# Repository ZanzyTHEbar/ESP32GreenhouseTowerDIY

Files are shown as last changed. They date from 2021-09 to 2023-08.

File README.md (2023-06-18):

   

# :seedling: ESP32GreenhouseTowerDIY :seedling:

This repo is dedicated to the **DIY ESP32** based automated *Aeroponic* or *Hydroponic* Modular Tower Garden :cactus: .

# WHAT IS THIS PROJECT

In the height of COVID I wanted to grow my own food indoors. This open source project is a culmination of my own work and many inspirations from the internet to develop an easy, approachable and beginner friendly project for hobbyists.

This project is designed to be modular and affordable. Featuring a vertical tower system with interlocking parts and an adapter to a common `20L/5gallon` bucket.

The design also features an optional 3D printable Aeroponics Nozzle for converting the system from hydroponic to aeroponics.  

> I originally decided to go with an ESP32 using Micropython firmware. While Arduino is perfectly fine, i wanted this project to be approachable to all skill levels, python seemed like the most common first "language". However, I since realized that most people who use this _won't_ be coding themselves and i prefer C++ more than python, so I switched the entire project over and am building a website to flash the boards. Users will not need to download any code themselves. Please stay tuned for the documentation website.  
>
> **Note**: I have added Arduino Core support for the ESP32. This is a work in progress and will is now the main code-base. It simply has more sensor support, a few more features, and it runs faster/consumes less power.

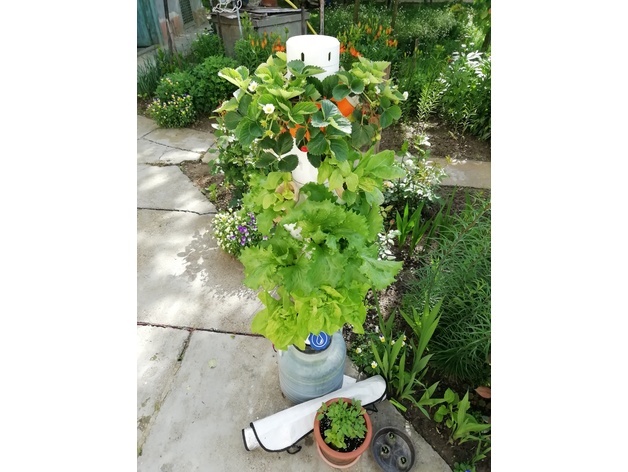
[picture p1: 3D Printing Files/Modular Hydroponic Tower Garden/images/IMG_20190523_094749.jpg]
tower garden


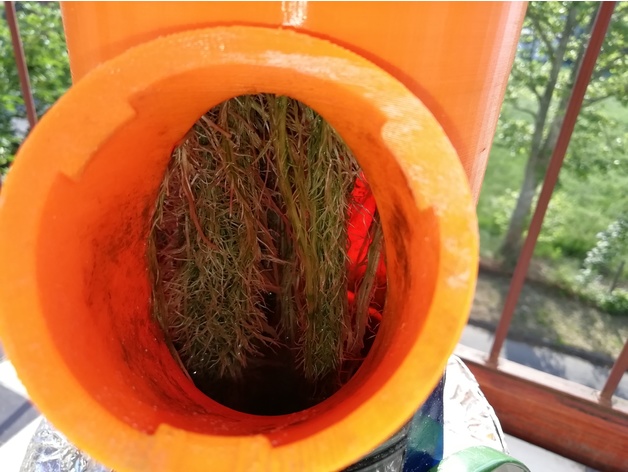
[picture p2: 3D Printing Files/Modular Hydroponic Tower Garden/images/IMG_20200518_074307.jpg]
tower garden


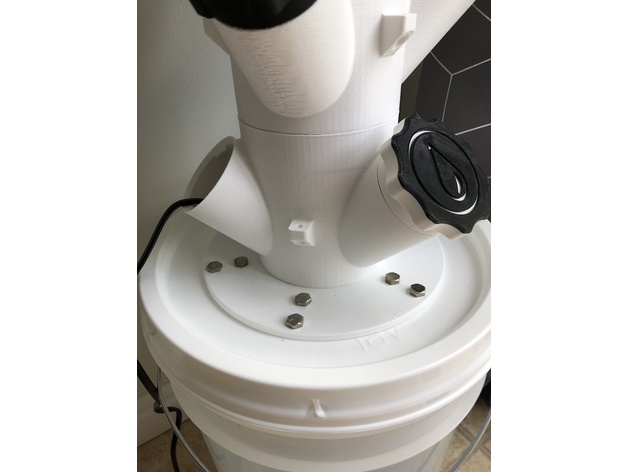
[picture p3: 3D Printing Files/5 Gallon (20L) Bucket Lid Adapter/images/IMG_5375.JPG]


# HOW TO ORDER PCBS

PCBS can be ordered from [JLCPCB](https://jlcpcb.com/) or [PCBWay](https://www.pcbway.com/), or made yourself. The PCB files are still in prototype phase and I welcome any development ideas.

# Introduction

**Purpose:** These are instructions to build an open hardware, DIY Vertical Greenhouse Garden.

**Expected results:** A fully functional and (reasonably) automated vertical tower system.

**Minimal parts cost:** `<$20` for the basic system which consists of a `20L/5gallon` (can be smaller - minimum size is `4L/1gallon`) humidifier box/water reservoir and submersible pump - about `$100`. You will also need to purchase the PCB's `~$40`, power supply and sensors `~$30`. The cost of the parts will vary depending on the size of the tower, and the number of sensors. The cost of 3D printing the tower will be `~$25` or less. The full `1m` tower consumes `~2kg` of `PETG` - which is the recommended printing material for outdoor use. The tower can be printed in `ABS` and/or `PETG` materials.

> **Note**: The cost of plant nutrients is not taken into account, and is up to you to control.

**Goal:** The goal of this project was to build a high-efficiency, very low cost direct DIY vertical tower garden for growing small fruits and vegetables.

____

> **Warning**: The sections below are experimental docs and are subject to change. Please wait for the documentation website to be finished if you want a consistent experience.

## How to Setup  - Hardware

Setup is very straight forward, thankfully. You will need to purchase a few components before you begin:

### ***Materials for purchase***

1. Raspberrypi - *any model*
   1. Install the MQTT client included with Home Assistant (install Home Assistant), as this project has full support for Home Assistant (Arduino Core version only currently).
      1. Alternatively, you can install Mosquitto broker to the pi and connect it to your network
2. 12V submersible water pump
3. 3m or more of Vinyl tubing with 10mm ID and 13mm OD

____

## How to Setup - Software

1. Acquire all parts and ESP32 (WROVER and WROOM (S3 versions are supported) have both been tested).
2. Acquire The remaining sensors and components - assemble

### ***SETUP***

____

#### Micropython

1. Plug ESP32 into computer - open your IDE (i used Thonny for this project) Flash the micropython firmware to the esp32
   1. Upload ESP32MicropytyhonLibraries ---> rename to ESP32Micro
   2. Upload boot.py and greenhouse.py to root directory

____

#### Arduino Core

1. Plug ESP32 into computer - navigate to [WebSerial](/ESP32GreenhouseTowerDIY/webserial/)
   1. Configure your chosen sensors and features
   2. Press build and upload, and wait for the green light to turn on - it is safe to unplug the ESP32 at that point.

____

#### MQTT Broker Configuration and Connection

If you have chosen the mDNS option, you will need to setup mDNS on your network for MQTT Discovery. The mDNS service on the ESP is already configure, if you chose that feature, and should appear on your network as at the `<name>.tower.local` address.

The MQTT Broker is a free service that allows you to publish and subscribe to MQTT messages. To automate the connection process, this project offers Multi-Cast DNS (mDNS/Zeroconf) to find the broker. For this to work, you must have a broker on your local network, and you must have only 1 MQTT broker within the range of the client, otherwise the client will simply connect to the images broker it finds.

Using a Zeroconf approach we can avoid having to hard code the broker's IP address or hostname into the client device's firmware. Instead we can use DNS-SD and Avahi/Bonjour to discover the server hosting the MQTT broker.

To enable MQTT discovery on the broker, simply install avahi-daemon.

##### Option One:

If you are using Home Assistant, you can use the MQTT Discovery feature within the firmware, and the MQTT broker will be discovered automatically. Nothing is needed from you for this to work. Simply turn on the ESP32 and have the `mDNS` feature enabled in the firmware.

You can refer to the [ZeroConf Documentation here](https://www.home-assistant.io/integrations/zeroconf/) and [here](https://developers.home-assistant.io/docs/creating_integration_manifest/#zeroconf) for home assistance for more information and troubleshooting.

If for some reason you are unable to use the MQTT Discovery feature, you can still use the mDNS feature to discover the broker, see Option Two below.

##### Option Two:

You will need to install the [avahi](https://avahi.org/) package. For a Raspberry Pi, use the following command:

    sudo apt-get install avahi-daemon

For this to work, the MQTT service needs to be advertised. On a Linux host system, Avahi can be configured to do this by including the following in `/etc/avahi/services/mqtt.service`:

```xml
<!DOCTYPE service-group SYSTEM "avahi-service.dtd">
<service-group>
 <name replace-wildcards="yes">MQTT on %h</name>
  <service>
   <type>_mqtt._tcp</type>
   <port>1883</port>
  </service>
</service-group>
```

____

## Benefits

____

## Challenges and Limitations

____

## Safety Considerations

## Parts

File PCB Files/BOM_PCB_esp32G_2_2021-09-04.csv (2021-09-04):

ID | Name | Designator | Footprint | Quantity | Manufacturer Part | Manufacturer | Supplier | Supplier Part | Price | Pins | 3DModel | JLCPCB Part Class | Paste Type | Contributor | description | license | link
1 | PIN_Female_2 | DATA,POWER,U3,U6,U7 | PIN_CONNECTOR_2 | 5 | Buchsenleiste Femaile 24 |  |  |  |  | 2 |  |  |  | Florian1
2 | LL4148 | D6,D7,D8 | LL-34_L3.5-W1.5-RD-1 | 3 | LL4148 | SEMTECH | LCSC | C9808 | 0.007 | 2 | LL-34_L3.7-W1.6 | Basic Part |  | jiaowoxiaolu |  |  | https://item.szlcsc.com/289405.html
3 | PIN_Female_4 | U4 | PIN_CONNECTOR_2 | 1 | Buchsenleiste Femaile 24 |  |  |  |  | 2 |  |  |  | Florian1
4 | Header-Female-2.54_1x20 | P6,P7 | HDR-TH_20P-P2.54-V-F | 2 | 2.54mm 1*20P Female header | BOOMELE | LCSC | C50984 | 0.124 | 20 | HDR-F-2.54_1x20 | Extended Part |  | 立创EDA官方封装库 |  |  | https://item.szlcsc.com/316177.html
5 | TERMINAL_3P/5.08 | P1,P4,P5 | 5.08-3P_SCREW_TERMINAL | 3 | Screw terminal 3p |  |  |  |  | 3 |  |  |  | reino.forward
6 | TERMINAL_2P/5.08 | P2,P3 | 5.08-2P_SCREW_TERMINAL | 2 | Screw terminal 2p |  |  |  |  | 2 |  |  |  | Giuseppe Fusi
7 | 1N4007 | D4,D5 | DO-41_BD2.4-L4.7-P8.70-D0.9-RD | 2 | 1N4007 | SEMTECH | LCSC | C106903 | 0.015 | 2 | DO-41_D2.4-L4.7-P8.70 | Extended Part |  | 官方封装库 |  |  | https://item.szlcsc.com/85412.html
8 | 2N3904(SOT-23) | Q1,Q2 | SOT-23-3_L2.9-W1.3-P1.90-LS2.4-TR | 2 | 2n3904S-RTK/PS | KEC | LCSC | C18536 | 0.016 | 3 | SOT-23-3P_L2.9-W1.3-H1.0-LS2.4-P0.95 |  | SOT-23 | 立创EDA官方封装库 |  |  | https://item.szlcsc.com/70837.html
9 | LDR07 | R1 | RESISTOR_LDR_5.1X4.3_RM3.4 | 1 |  |  |  |  |  | 2 |  |  |  | KiCAD |  | https://www.gnu.org/licenses/lgpl-2.1.html
10 | 10k | R2,R3,R4,R5 | R0603 | 4 |  |  |  |  |  | 2 | R0603_L1.6-W0.8-H0.8 |  |  | 立创EDA官方封装库 |  |  | https://www.mouser.in/datasheet/2/447/PYu_RT_1_to_0_01_RoHS_L_11-1669912.pdf
11 | DHT11 | U5 | SENSOR-TH_DHT11 | 1 | CHT11 | CYBERSEN | LCSC | C476208 | 1.559 | 4 | SENSOR-TH_DHT11 | Extended Part |  | 立创EDA官方封装库 |  |  | https://list.szlcsc.com/catalog/922.html
12 | JQC-3FF-S-Z | U8,U9 | JQC-3FF-S-Z | 2 | JQC-3FF-S-Z |  |  |  |  | 5 |  |  |  | EasyEDA |  |  | https://www.alibaba.com/product-detail/relay-types-JQC-3FF-S-Z_60682592473.html
13 | LED-TH-5mm_R | LED1 | LED-TH_BD5.0_RED | 1 | 333-2SURD/S530-A3 | EVERLIGHT(台湾亿光) | LCSC | C87271 | 0.035 | 2 | LED-TH_BD5.0_Red |  |  | LCEDA_Lib
14 | LED-TH-5mm_G | LED2 | LED-TH_BD5.0_GREEN | 1 | 333-2SYGD/S530-E2 | EVERLIGHT(台湾亿光) | LCSC | C88163 | 0.037 | 2 | LED-TH_BD5.0_Green |  |  | LCEDA_Lib
15 | LED-TH-5mm_B | LED3 | LED-TH_BD5.0_BLUE | 1 |  |  | LCSC |  |  | 2 | LED-TH_BD5.0_Blue |  |  | LCEDA_Lib
16 | 220Ohm | R6,R7,R8 | R0603 | 3 |  |  |  |  |  | 2 | R0603_L1.6-W0.8-H0.8 |  |  | LCEDA_Lib |  |  | https://www.mouser.in/datasheet/2/447/PYu_RT_1_to_0_01_RoHS_L_11-1669912.pdf

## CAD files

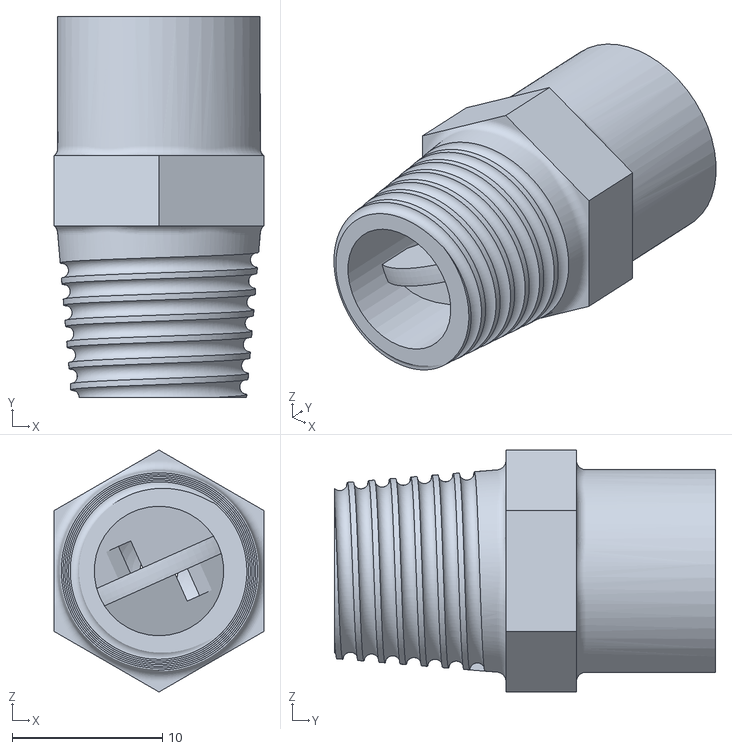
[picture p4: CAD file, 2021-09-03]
3D Printing Files/Aeroponic Misting Nozzles/files/Full_cone_spray_nozzle.STL
14.0 x 25.4 x 16.1

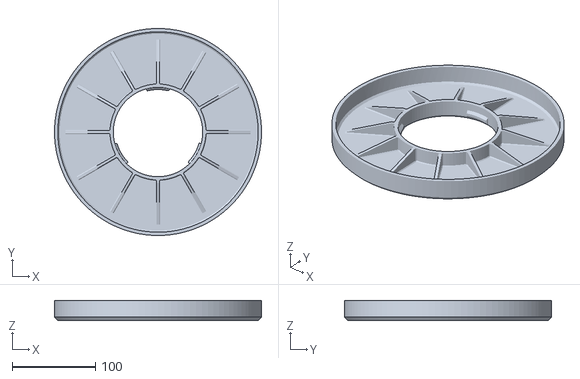
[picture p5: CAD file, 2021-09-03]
3D Printing Files/Modular Hydroponic Tower Garden/files/IKEA_Muskot_Pot_7_12_Adapter_ID240mm_Full.STL
248.0 x 248.0 x 24.0

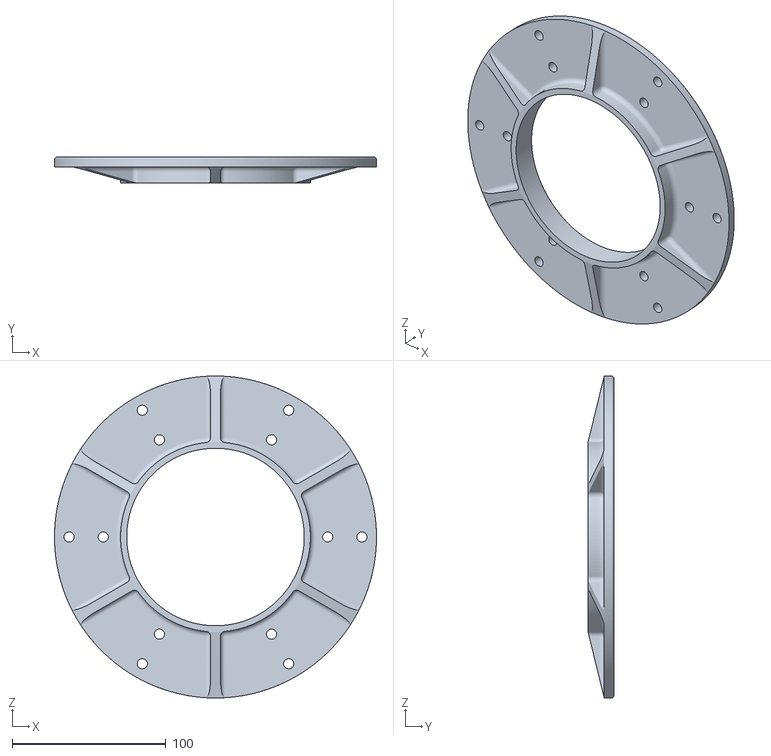
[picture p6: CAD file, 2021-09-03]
3D Printing Files/5 Gallon (20L) Bucket Lid Adapter/files/5_gallon_bucket_lid_Bottom_Adapter.STL
209.5 x 16.9 x 209.5

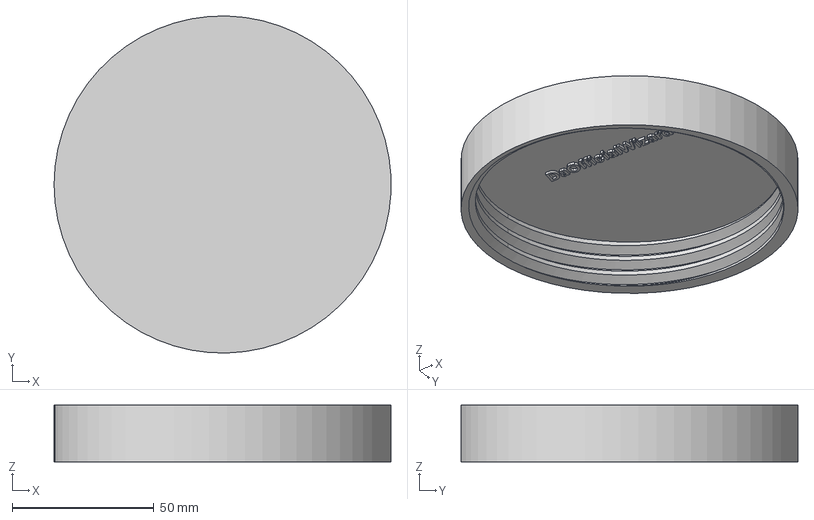
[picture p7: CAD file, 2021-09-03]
3D Printing Files/Aeroponic Misting Nozzles/files/lid v1.step
118.9 x 119.0 x 20.0 mm

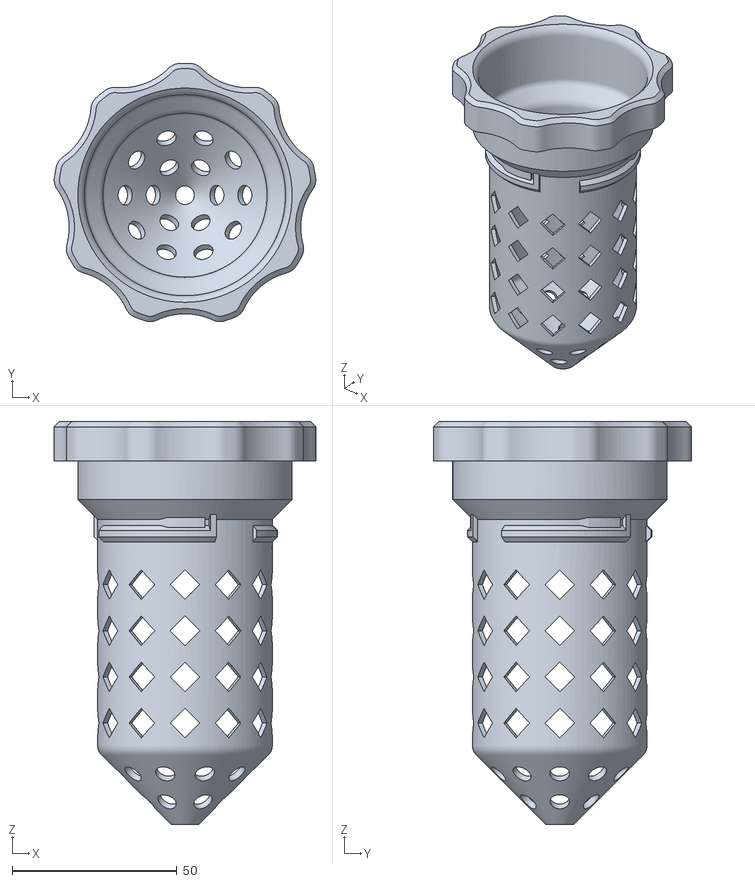
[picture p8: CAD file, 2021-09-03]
3D Printing Files/Modular Hydroponic Tower Garden/files/Standard_Pot_02.STL
79.4 x 78.4 x 122.3

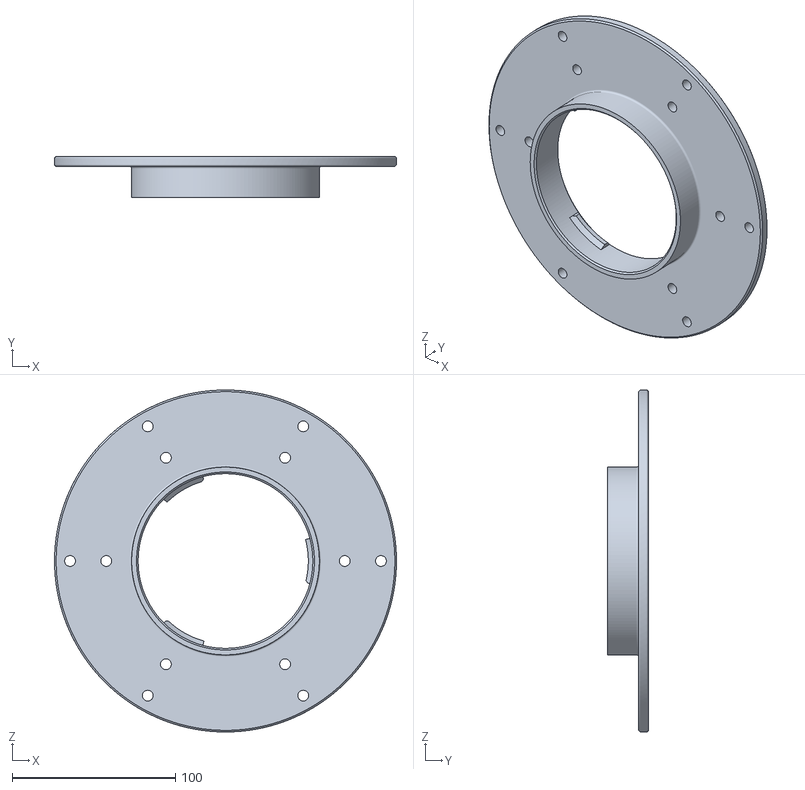
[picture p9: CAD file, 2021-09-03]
3D Printing Files/5 Gallon (20L) Bucket Lid Adapter/files/5_gallon_bucket_lid_Top_Adapter.STL
209.5 x 25.4 x 209.5

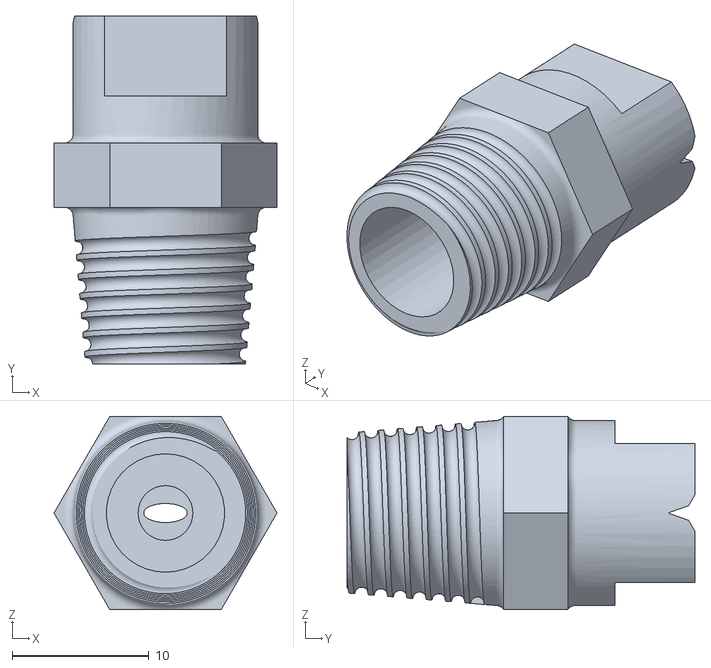
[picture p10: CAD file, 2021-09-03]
3D Printing Files/Aeroponic Misting Nozzles/files/Flat_spray_nozzle.STL
16.3 x 25.4 x 14.1

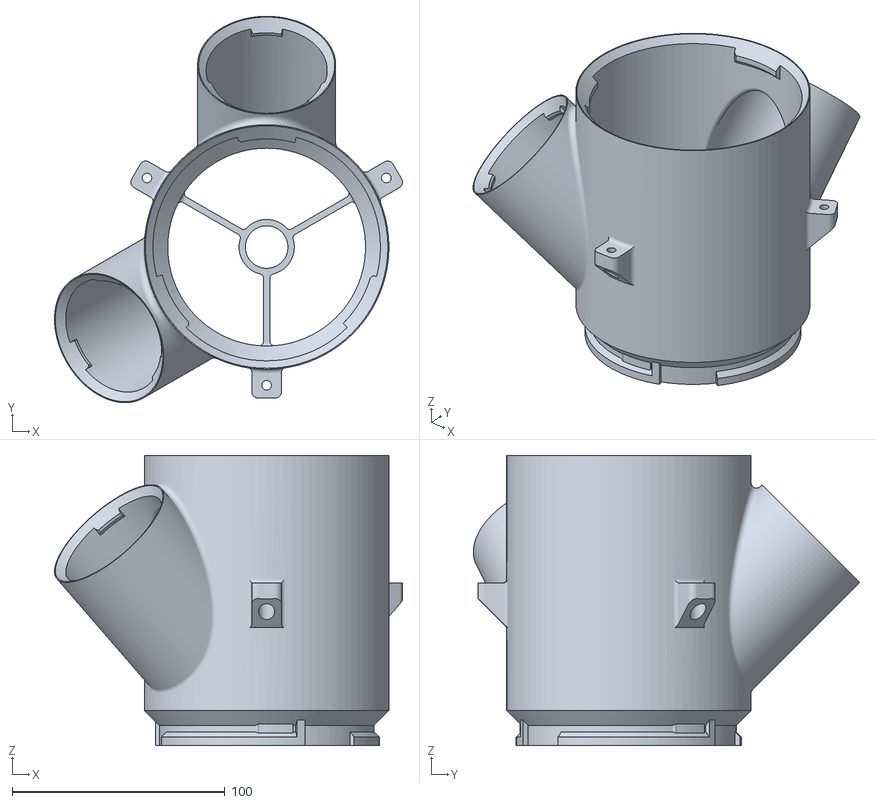
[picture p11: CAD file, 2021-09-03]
3D Printing Files/Modular Hydroponic Tower Garden/files/2-Way_Planting_Module_Hollow.STL
163.7 x 181.7 x 136.5

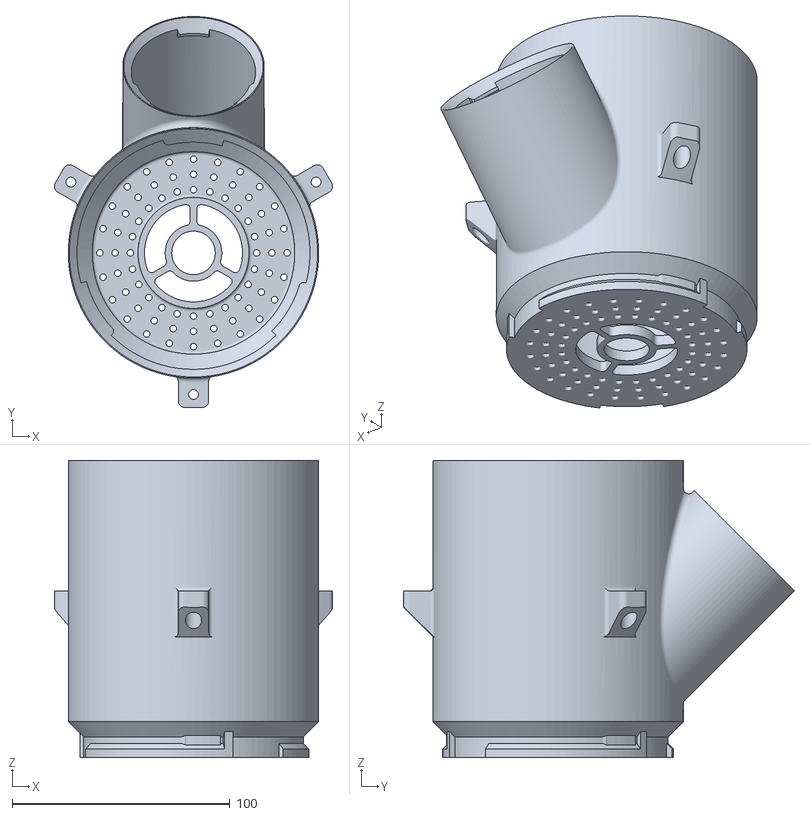
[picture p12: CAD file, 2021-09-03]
3D Printing Files/Modular Hydroponic Tower Garden/files/1-Way_Planting_Module.STL
127.8 x 179.5 x 136.5

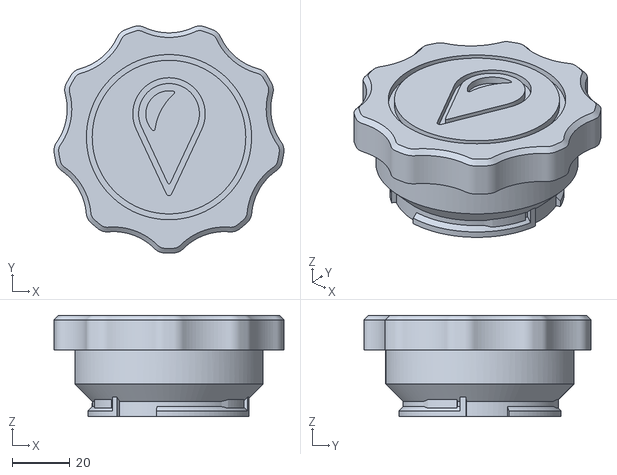
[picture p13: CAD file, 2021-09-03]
3D Printing Files/Modular Hydroponic Tower Garden/files/Filling_Cap.STL
79.4 x 78.4 x 35.0

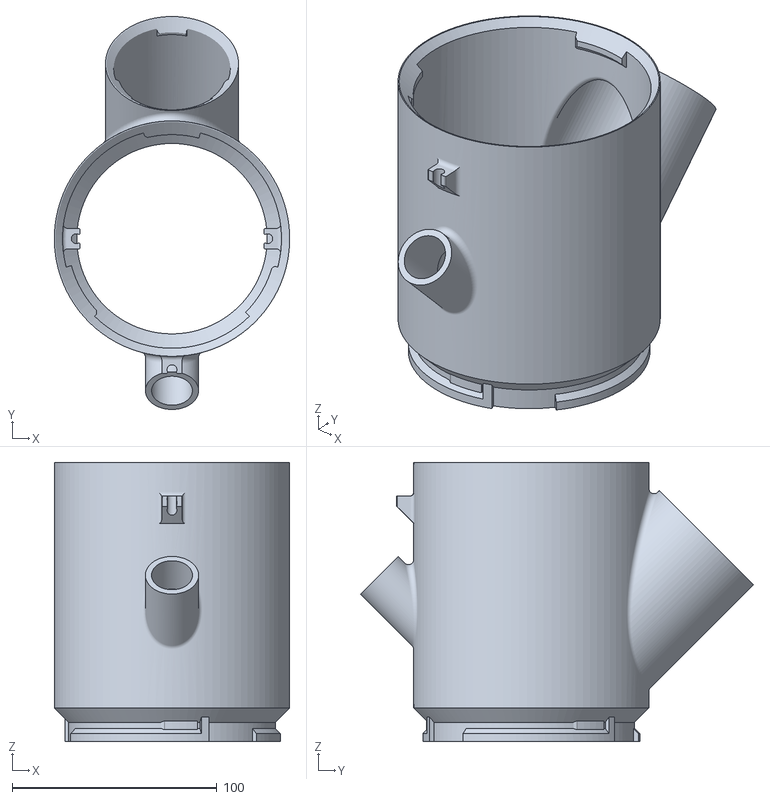
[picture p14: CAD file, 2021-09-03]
3D Printing Files/Modular Hydroponic Tower Garden/files/Filling_Module_mod_01.STL
114.9 x 192.0 x 136.5

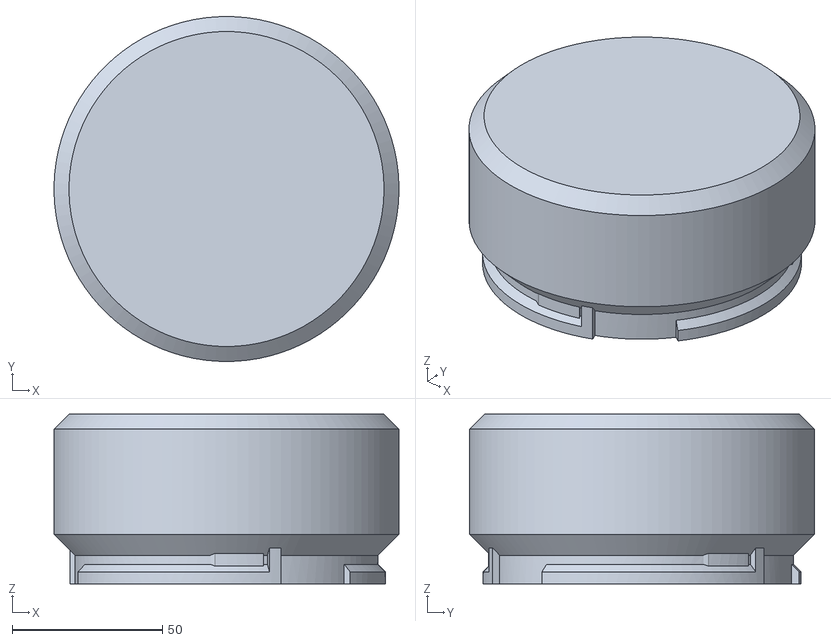
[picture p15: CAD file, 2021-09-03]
3D Printing Files/Modular Hydroponic Tower Garden/files/Lid_Without_Holes.STL
114.9 x 115.0 x 56.5

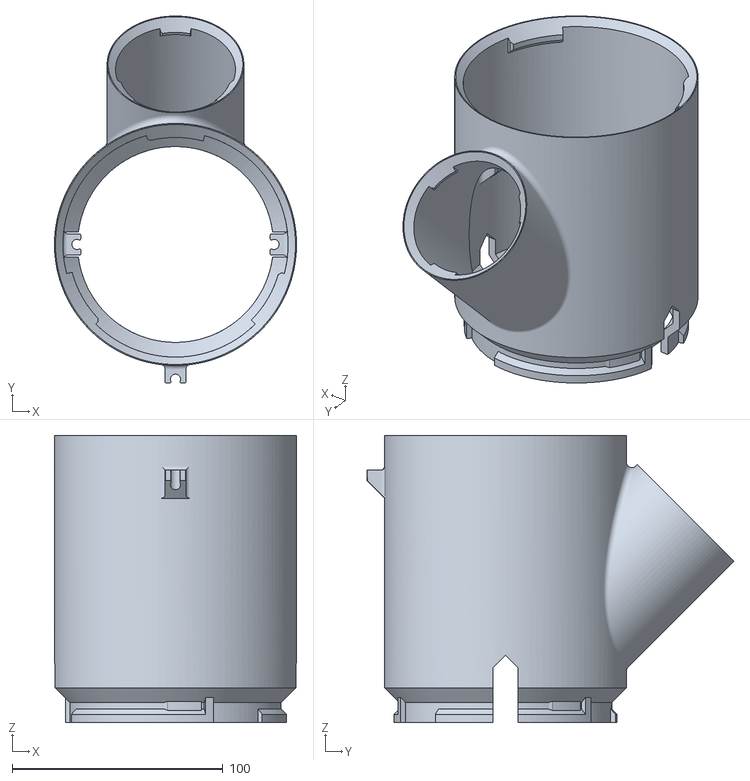
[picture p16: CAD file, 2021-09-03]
3D Printing Files/Modular Hydroponic Tower Garden/files/Filling_Module_Cut_mod_01.STL
115.0 x 174.3 x 136.5

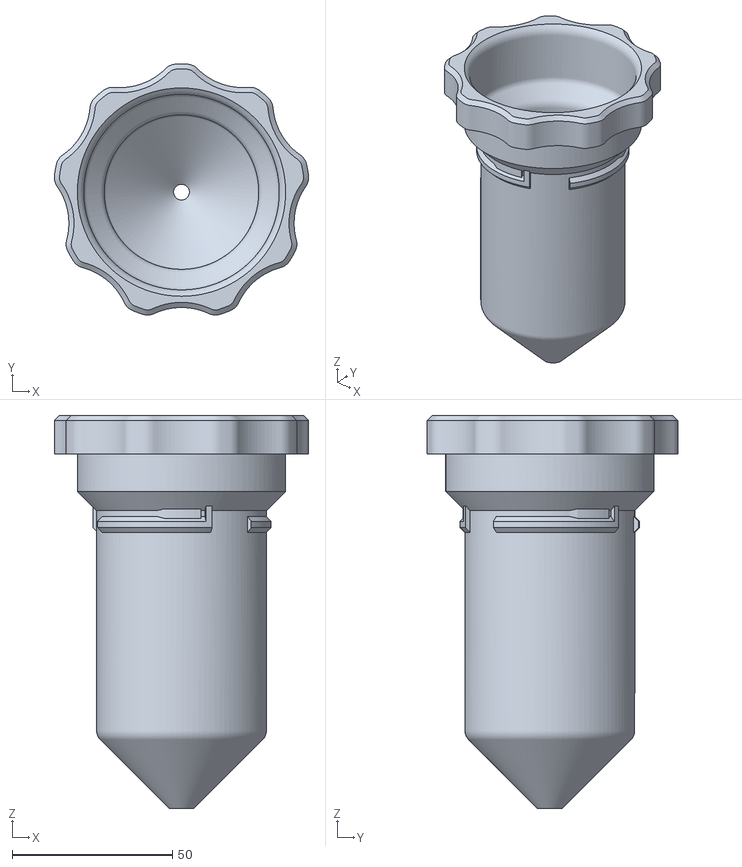
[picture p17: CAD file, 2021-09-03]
3D Printing Files/Modular Hydroponic Tower Garden/files/Standard_Pot_Raw.STL
79.4 x 78.4 x 122.6

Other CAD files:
3D Printing Files/Modular Hydroponic Tower Garden/files/2-Way_Planting_Module_Hollow_Without_M3.STL
3D Printing Files/Modular Hydroponic Tower Garden/files/Jiffy-7_41_Pot_For_4-5-Way_Planting_Module.STL
3D Printing Files/Modular Hydroponic Tower Garden/files/Module_Spacer_40mm.STL
3D Printing Files/Modular Hydroponic Tower Garden/files/Blank_Cap.STL
3D Printing Files/Modular Hydroponic Tower Garden/files/1-Way_Planting_Module_Hollow.STL
3D Printing Files/Modular Hydroponic Tower Garden/files/1-Way_Planting_Module_Hollow_Without_M3.STL
3D Printing Files/Modular Hydroponic Tower Garden/files/3-Way_Planting_Module_Hollow.STL
3D Printing Files/Modular Hydroponic Tower Garden/files/3-Way_Planting_Module_Hollow_Without_M3.STL
3D Printing Files/Modular Hydroponic Tower Garden/files/4-Way_Planting_Module_Hollow.STL
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

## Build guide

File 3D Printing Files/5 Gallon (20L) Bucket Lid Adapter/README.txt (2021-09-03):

5 Gallon Bucket Lid Adapter Plates by Trevorhirschi on Thingiverse: https://www.thingiverse.com/thing:4395675

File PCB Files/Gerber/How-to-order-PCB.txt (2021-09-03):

How to Order PCB

Please refer to:
https://docs.easyeda.com/en/PCB/Order-PCB

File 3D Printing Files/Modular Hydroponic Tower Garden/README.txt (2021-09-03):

Modular Hydroponic Tower Garden by boundarycondition on Thingiverse: https://www.thingiverse.com/thing:3405964

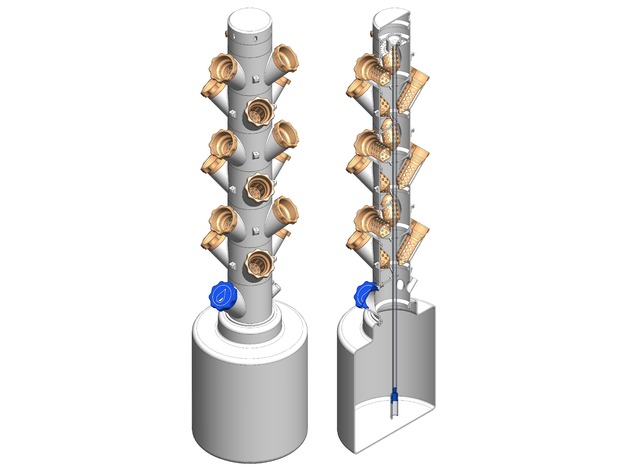
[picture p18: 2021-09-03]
3D Printing Files/Modular Hydroponic Tower Garden/images/MHTG_V113_03.png

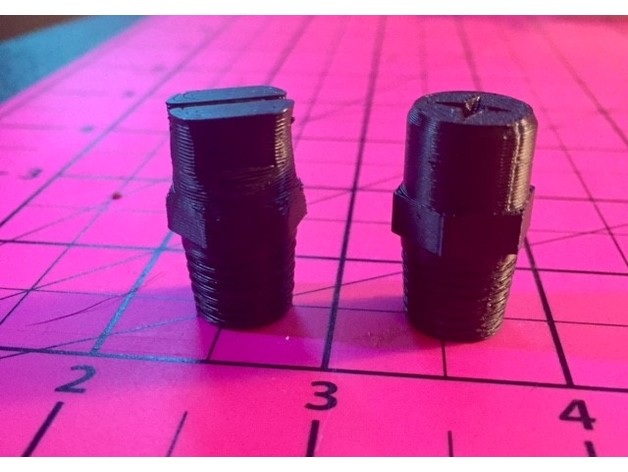
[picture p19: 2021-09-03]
3D Printing Files/Aeroponic Misting Nozzles/images/a0927398989d4c5b18c56880bd56442b_preview_featured.jpg

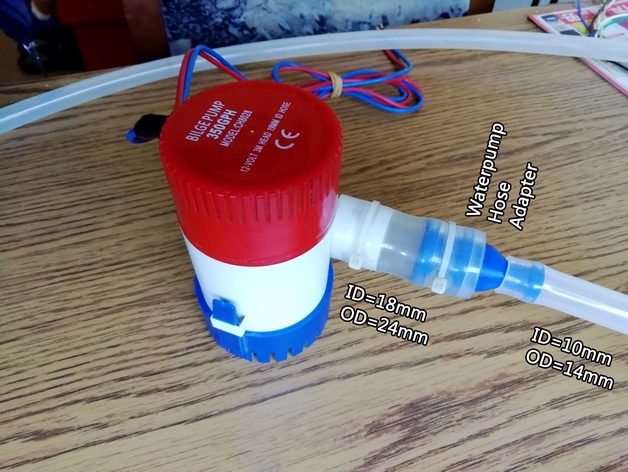
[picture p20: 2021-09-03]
3D Printing Files/Modular Hydroponic Tower Garden/images/IMG_20190920_124431_02.jpg

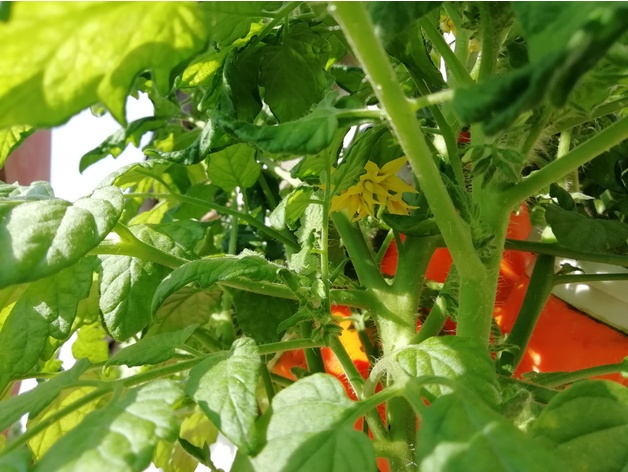
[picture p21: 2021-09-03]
3D Printing Files/Modular Hydroponic Tower Garden/images/IMG_20200518_074239.jpg

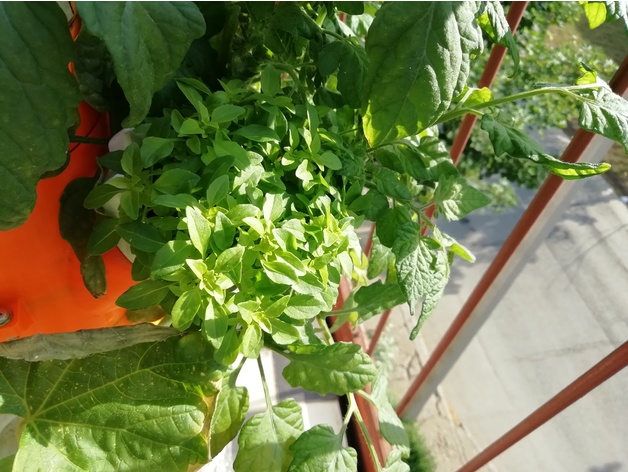
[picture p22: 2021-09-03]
3D Printing Files/Modular Hydroponic Tower Garden/images/IMG_20200518_074503.jpg

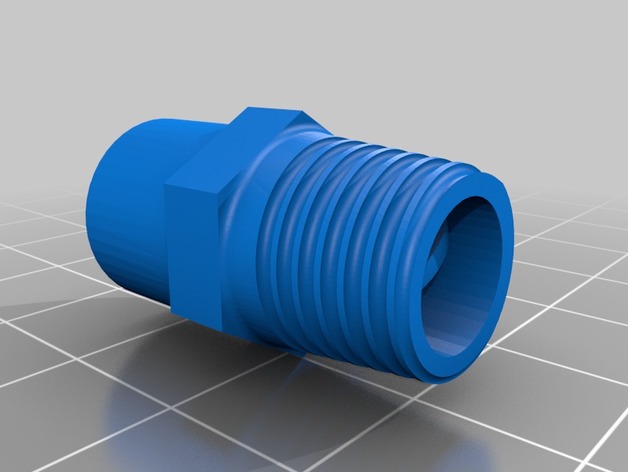
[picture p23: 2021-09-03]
3D Printing Files/Aeroponic Misting Nozzles/images/b3a1b81c2451a407eea475d162c24e25_preview_featured.jpg

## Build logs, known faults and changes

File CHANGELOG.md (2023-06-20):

# 📦 Changelog 


> All notable changes to this project will be documented in this file

## [1.2.0](https://github.com/ZanzyTHEbar/ESP32GreenhouseTowerDIY/compare/v1.1.3...v1.2.0) (2023-06-20)

### 🍕 Features

* begin working on the API ([271a828](https://github.com/ZanzyTHEbar/ESP32GreenhouseTowerDIY/commit/271a8285c2cfdbf2701d9e2129c0c9203dac1db0))

## [1.1.3](https://github.com/ZanzyTHEbar/ESP32GreenhouseTowerDIY/compare/v1.1.2...v1.1.3) (2023-06-20)

### 🐛 Bug Fixes

* bug in serializer ([8999751](https://github.com/ZanzyTHEbar/ESP32GreenhouseTowerDIY/commit/8999751c1dfa226e95007fec7c210f5b7b87d3ce))

## [1.1.2](https://github.com/ZanzyTHEbar/ESP32GreenhouseTowerDIY/compare/v1.1.1...v1.1.2) (2023-06-20)

### 🧑‍💻 Code Refactoring

* Update user_config.ini ([a0a9ad5](https://github.com/ZanzyTHEbar/ESP32GreenhouseTowerDIY/commit/a0a9ad5e9ebc33352586a8f6efbfea676100db00))

## [1.1.1](https://github.com/ZanzyTHEbar/ESP32GreenhouseTowerDIY/compare/v1.1.0...v1.1.1) (2023-06-20)

### 🧑‍💻 Code Refactoring

* cleanup serializer ([f33a53d](https://github.com/ZanzyTHEbar/ESP32GreenhouseTowerDIY/commit/f33a53db516d198f2b167e444611039c36365094))

## [1.1.0](https://github.com/ZanzyTHEbar/ESP32GreenhouseTowerDIY/compare/v1.0.0...v1.1.0) (2023-06-18)

### 📝 Documentation

* Update README.md ([b944241](https://github.com/ZanzyTHEbar/ESP32GreenhouseTowerDIY/commit/b9442412ac55b0a36576bca5d22c3aadfa2c6640))

## 1.0.0 (2023-06-18)

### 🍕 Features

* add background task handler ([7f9d965](https://github.com/ZanzyTHEbar/ESP32GreenhouseTowerDIY/commit/7f9d9652ec51188cecebfd2e776007dd5767e54a))
* add logo to serial console ([169f136](https://github.com/ZanzyTHEbar/ESP32GreenhouseTowerDIY/commit/169f136b43dbdc34171118e671f1ee006935b9f4))
* add removeRelay ([aa6b9fd](https://github.com/ZanzyTHEbar/ESP32GreenhouseTowerDIY/commit/aa6b9fdf42b4f89757626d063ef28ee81243c39f))
* begin adding config ([247ad1b](https://github.com/ZanzyTHEbar/ESP32GreenhouseTowerDIY/commit/247ad1b8340b6e50109b7cb38dd77d7dc162f690))
* begin adding support for HASSIO ([f4a4006](https://github.com/ZanzyTHEbar/ESP32GreenhouseTowerDIY/commit/f4a4006fc36a378f9ec4ef652aeb424996f39a81))
* begin integrating background task manager ([611c732](https://github.com/ZanzyTHEbar/ESP32GreenhouseTowerDIY/commit/611c732598700a5a34641902c8e5e711c8793e47))
* i2c relay support ([c4b1cbb](https://github.com/ZanzyTHEbar/ESP32GreenhouseTowerDIY/commit/c4b1cbb55e8c29d10ea52566124e868feb2827f1))
* impl addRelay to api ([4e2c73f](https://github.com/ZanzyTHEbar/ESP32GreenhouseTowerDIY/commit/4e2c73f5ceaf15676d1a19be52be850a3a7c978f))
* overhaul config and tasks ([ff72244](https://github.com/ZanzyTHEbar/ESP32GreenhouseTowerDIY/commit/ff7224402902e162c923145cfe91ff86677751ea))
* setup refactoring, ci, and inis ([bad1ce1](https://github.com/ZanzyTHEbar/ESP32GreenhouseTowerDIY/commit/bad1ce1ed972c39e2f4ed75582dfc6000104231e))
* still working ([59022bf](https://github.com/ZanzyTHEbar/ESP32GreenhouseTowerDIY/commit/59022bf026c27d1fa8b6bcfb275aec0f4755df3e))
* update to newest network manager ([2539854](https://github.com/ZanzyTHEbar/ESP32GreenhouseTowerDIY/commit/253985408ced2049fb47e36dd6fde1e0742f3db0))

### 🐛 Bug Fixes

* add  mqtt client visitor ([008b079](https://github.com/ZanzyTHEbar/ESP32GreenhouseTowerDIY/commit/008b0793ece18bd0a37ea9847559e57404752caf))
* add removeRelay to api ([15feaf4](https://github.com/ZanzyTHEbar/ESP32GreenhouseTowerDIY/commit/15feaf4829c70c66a4eb47b02abc6f7a642066d5))
* add start state to relays ([edd2801](https://github.com/ZanzyTHEbar/ESP32GreenhouseTowerDIY/commit/edd2801c6a9a63cb19ba3c8e9ec0b5e79bc07e81))
* add timer to accumulatedata ([e90dffb](https://github.com/ZanzyTHEbar/ESP32GreenhouseTowerDIY/commit/e90dffb40a55c989c338791ef1b1b8ff8b91151f))
* begin refactoring code-base ([584bfaa](https://github.com/ZanzyTHEbar/ESP32GreenhouseTowerDIY/commit/584bfaa4a164f5f6a2a31f217db52fe18ec87216))
* begin simplifying and refactoring ([de9b670](https://github.com/ZanzyTHEbar/ESP32GreenhouseTowerDIY/commit/de9b6702342b0255bb6ba55b76eb7a2769c9dcd9))
* begin to refactor mqtt stack ([0bd8ff9](https://github.com/ZanzyTHEbar/ESP32GreenhouseTowerDIY/commit/0bd8ff90b524144a5a89fcba01a43d935ebe4166))
* bug in sensor serializer formatter ([26774af](https://github.com/ZanzyTHEbar/ESP32GreenhouseTowerDIY/commit/26774af5ab9e76a8dbb24303746e92ce84d81aa9))
* cleanup project structure ([f25b43a](https://github.com/ZanzyTHEbar/ESP32GreenhouseTowerDIY/commit/f25b43a0ad60696e15e5fafdd2175d03ef090d4a))
* compile error ([59a20ac](https://github.com/ZanzyTHEbar/ESP32GreenhouseTowerDIY/commit/59a20ac7c945881f59689965ba0dd4c5813decdf))
* compile error ([c57898d](https://github.com/ZanzyTHEbar/ESP32GreenhouseTowerDIY/commit/c57898dc30a83b830c8c30cc643561f615cf4178))
* compile errors ([7fdde7b](https://github.com/ZanzyTHEbar/ESP32GreenhouseTowerDIY/commit/7fdde7bbe970b10dafe5ef1c940fdfbc5f1e67f8))
* compile time bug ([92ab0e8](https://github.com/ZanzyTHEbar/ESP32GreenhouseTowerDIY/commit/92ab0e804696751d60af7a1266743a8189cb0d1f))
* continue fixing sensors ([ef98748](https://github.com/ZanzyTHEbar/ESP32GreenhouseTowerDIY/commit/ef98748f7f96cf03727c0a6a054240d080ade9e8))
* continue making edits ([f0f1323](https://github.com/ZanzyTHEbar/ESP32GreenhouseTowerDIY/commit/f0f13238a6e6fff713a0265e0bcfe2a4fc8f7e4e))
* continue refactoring code-base ([dcb3d75](https://github.com/ZanzyTHEbar/ESP32GreenhouseTowerDIY/commit/dcb3d75798599deaa3c4a6bd21f0178e0fb71aa7))
* continue refactoring code-base ([2bdc1b8](https://github.com/ZanzyTHEbar/ESP32GreenhouseTowerDIY/commit/2bdc1b8bc0cd16e176e3e6bd1cf0368c96c52355))
* continue working on mqtt stack ([c42d9c4](https://github.com/ZanzyTHEbar/ESP32GreenhouseTowerDIY/commit/c42d9c44ec2d3325caae869295da1b01f16bf78e))
* enable mqtt loop ([9418456](https://github.com/ZanzyTHEbar/ESP32GreenhouseTowerDIY/commit/94184566956d98a0f5e28d0d27f130e73efc7507))
* fix api command handlers ([3327887](https://github.com/ZanzyTHEbar/ESP32GreenhouseTowerDIY/commit/3327887e54671d9dce614896bef62d040ebe90c0))
* fix api command handlers ([0a0f806](https://github.com/ZanzyTHEbar/ESP32GreenhouseTowerDIY/commit/0a0f806283fb1280507ef1db9538304027100541))
* fix mqtt ([5c51c21](https://github.com/ZanzyTHEbar/ESP32GreenhouseTowerDIY/commit/5c51c212548154e2690fdf2c89ba7b476a53f419))
* fixing compile time errors due to refactor ([365d2ff](https://github.com/ZanzyTHEbar/ESP32GreenhouseTowerDIY/commit/365d2ff2c6c855ba025ef2729a9592680cc635de))
* github ignore case ([3996e54](https://github.com/ZanzyTHEbar/ESP32GreenhouseTowerDIY/commit/3996e541ccd244a9a5045c793d63810bb504932a))
* humidity json formatter ([df3ce56](https://github.com/ZanzyTHEbar/ESP32GreenhouseTowerDIY/commit/df3ce56cad9ae93e9cd550c7cfeae1391fe27b2a))
* implement ntp into visitor pattern ([ec15a6d](https://github.com/ZanzyTHEbar/ESP32GreenhouseTowerDIY/commit/ec15a6d86601800e3a94d1d309765debdfac75f1))
* implement ntp into visitor pattern ([01f636b](https://github.com/ZanzyTHEbar/ESP32GreenhouseTowerDIY/commit/01f636b7d49fffe0bda718e6e8f787afa00e2d53))
* json formatting for humidity sensor ([ee893ac](https://github.com/ZanzyTHEbar/ESP32GreenhouseTowerDIY/commit/ee893ace5fce674e574a0c613f118ccdbec9c43f))
* migrate old files ([7cdb34a](https://github.com/ZanzyTHEbar/ESP32GreenhouseTowerDIY/commit/7cdb34a376593182c0bd6f17a1585d215412d722))
* migrate to visitor pattern ([1bd1bc6](https://github.com/ZanzyTHEbar/ESP32GreenhouseTowerDIY/commit/1bd1bc69e6a3cc6db1d1e1be075842b6901ee374))
* mqtt class ([c1f8194](https://github.com/ZanzyTHEbar/ESP32GreenhouseTowerDIY/commit/c1f8194c59a89c9cf42f8ab0adb4160510b2a29f))
* mqtt handler ([57f2336](https://github.com/ZanzyTHEbar/ESP32GreenhouseTowerDIY/commit/57f23365ca524200709f9045cd673a6e61a76025))
* network lib dependancy ([a863db5](https://github.com/ZanzyTHEbar/ESP32GreenhouseTowerDIY/commit/a863db5becb4ef52df80d4b6a1409ab43577338b))
* refactor HASwitch's ([0803795](https://github.com/ZanzyTHEbar/ESP32GreenhouseTowerDIY/commit/080379553b2ec23fa7202dbc2dd199198b6d17ba))
* runtime crashing issue ([0dbeb00](https://github.com/ZanzyTHEbar/ESP32GreenhouseTowerDIY/commit/0dbeb0009ba8aff0ad46a5e90c2b0022f663f13e))
* simplify mqtt ([6a90967](https://github.com/ZanzyTHEbar/ESP32GreenhouseTowerDIY/commit/6a90967a27a603a6ae651852109e3833ee938abb))
* update ntp class to cpp string ([77c10c3](https://github.com/ZanzyTHEbar/ESP32GreenhouseTowerDIY/commit/77c10c32b788e3d80dee92ff4c37dd66ca36e321))

### 📝 Documentation

* setting up uml diagram ([46fae88](https://github.com/ZanzyTHEbar/ESP32GreenhouseTowerDIY/commit/46fae88a9499d9573cb7490f974bf572ac247fec))

### 🧑‍💻 Code Refactoring

* add logging ([8f193a4](https://github.com/ZanzyTHEbar/ESP32GreenhouseTowerDIY/commit/8f193a49e6c983112ce854be5c7c40b4fba00f39))
* begin to factor our defines ([e641e0a](https://github.com/ZanzyTHEbar/ESP32GreenhouseTowerDIY/commit/e641e0a6d7df69798441ae0cb3422ea4a3643d58))
* change mqtt client ([0b52b79](https://github.com/ZanzyTHEbar/ESP32GreenhouseTowerDIY/commit/0b52b7925438cc42fe2330338bf3f2a339ef564c))
* change mqtt client ([0314646](https://github.com/ZanzyTHEbar/ESP32GreenhouseTowerDIY/commit/0314646071b6887822d493dd5a0d7f475997d083))
* cleaning up project ([556b131](https://github.com/ZanzyTHEbar/ESP32GreenhouseTowerDIY/commit/556b13148539f271018cc8a0223dab23e9232e92))
* cleaning up some code ([32f7f78](https://github.com/ZanzyTHEbar/ESP32GreenhouseTowerDIY/commit/32f7f783e8e50064346792648b0ae970890f394a))
* cleanup humidity serializer ([fa12f1f](https://github.com/ZanzyTHEbar/ESP32GreenhouseTowerDIY/commit/fa12f1f6bb62a6a710698b5daa184df1868198b0))
* continue refactoring codebase ([c19cdaa](https://github.com/ZanzyTHEbar/ESP32GreenhouseTowerDIY/commit/c19cdaa794817658802f144bca5092660d83dd98))
* format ([7c9d0c4](https://github.com/ZanzyTHEbar/ESP32GreenhouseTowerDIY/commit/7c9d0c4aa561fe973a31b7a1eabc7af016cb065a))
* minor refactoring ([27dc688](https://github.com/ZanzyTHEbar/ESP32GreenhouseTowerDIY/commit/27dc688cc55856ee1f4ea10f6834cf58fa7f1684))
* move file structure ([9686433](https://github.com/ZanzyTHEbar/ESP32GreenhouseTowerDIY/commit/9686433bc97b8b087e833f835c4637797c870f43))
* refactor config ([78f0d6e](https://github.com/ZanzyTHEbar/ESP32GreenhouseTowerDIY/commit/78f0d6ea3db36369b0e36a4646da9d2f4837b638))
* remove networkState function ([e657dba](https://github.com/ZanzyTHEbar/ESP32GreenhouseTowerDIY/commit/e657dba58dc2aa7cce9036f65f8fe97e77e7cead))
* rename project directory ([be83203](https://github.com/ZanzyTHEbar/ESP32GreenhouseTowerDIY/commit/be83203ec80870f751e74649f8f8486c7c50b1bf))
* switch to specialization for sensor serializer ([868c7b8](https://github.com/ZanzyTHEbar/ESP32GreenhouseTowerDIY/commit/868c7b81d79d07dc434cd3184d5f2448f0c7cc6e))
* updating tasks ([bdacfae](https://github.com/ZanzyTHEbar/ESP32GreenhouseTowerDIY/commit/bdacfae8395808c8307538807a23319a0802dc0f))
* working on cleaning up code ([519cc1a](https://github.com/ZanzyTHEbar/ESP32GreenhouseTowerDIY/commit/519cc1a02d1d3f2b82dbadd64f2a1f9cfab31869))

### 🔁 Continuous Integration

* add environments to ci ([8de7e07](https://github.com/ZanzyTHEbar/ESP32GreenhouseTowerDIY/commit/8de7e07b6fbd442c9572beed04647415daf28b34))
* add todo ([6e4319f](https://github.com/ZanzyTHEbar/ESP32GreenhouseTowerDIY/commit/6e4319fe2e0d0dc310e13d7eb36a292b6c97a207))
* fix .relaserc ([818dd74](https://github.com/ZanzyTHEbar/ESP32GreenhouseTowerDIY/commit/818dd7404fc5c20b7a4140e1489bfc77333be8ef))
* fix ci archiving ([ecbf9be](https://github.com/ZanzyTHEbar/ESP32GreenhouseTowerDIY/commit/ecbf9be1a3423138f5c03c34ec0f3d2b0a7f89a2))
* fix ci archiving ([98bf6c5](https://github.com/ZanzyTHEbar/ESP32GreenhouseTowerDIY/commit/98bf6c528554d44570e8d0d65ebc6012fc912e98))
* fix ci archiving ([4a8f7c7](https://github.com/ZanzyTHEbar/ESP32GreenhouseTowerDIY/commit/4a8f7c7c11025cbb7c9ea4ad79adc9aed4ed1848))
* fix ci archiving ([db655ed](https://github.com/ZanzyTHEbar/ESP32GreenhouseTowerDIY/commit/db655edebd734e742322cf00818c3506d11520a9))
* setup ci pipeline ([484a2fd](https://github.com/ZanzyTHEbar/ESP32GreenhouseTowerDIY/commit/484a2fd2d66bc6ae4e30399550d0460500a729a3))
* setup ci pipeline ([ab5620d](https://github.com/ZanzyTHEbar/ESP32GreenhouseTowerDIY/commit/ab5620d3c29f631d47e450a37e2f4eae48a5923a))
* setup ci pipeline ([1a3f64b](https://github.com/ZanzyTHEbar/ESP32GreenhouseTowerDIY/commit/1a3f64b15beba70a4255e07a430656b16c5ec60a))
* setup ci pipeline ([658361c](https://github.com/ZanzyTHEbar/ESP32GreenhouseTowerDIY/commit/658361c78b55be2d5e40dc3f17d3576900d96c7f))

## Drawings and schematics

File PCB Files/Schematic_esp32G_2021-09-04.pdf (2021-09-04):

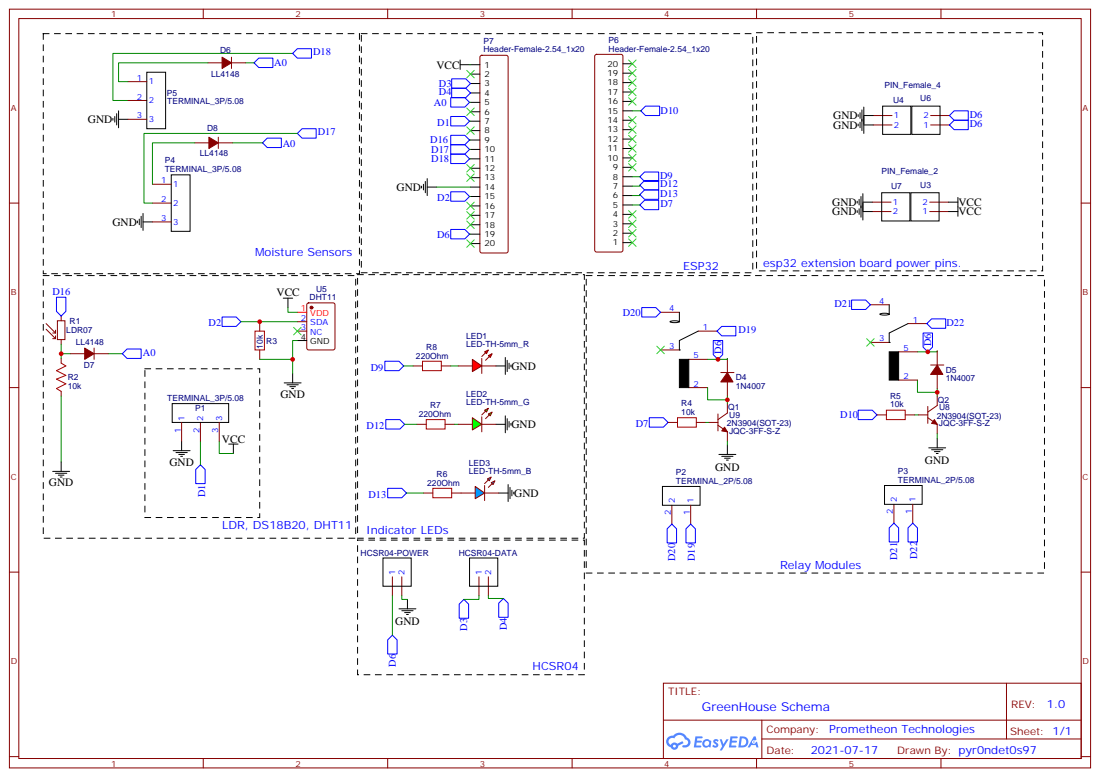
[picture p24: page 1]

esp32 extension board power pins.

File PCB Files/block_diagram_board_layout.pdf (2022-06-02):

## Board Design Architecture

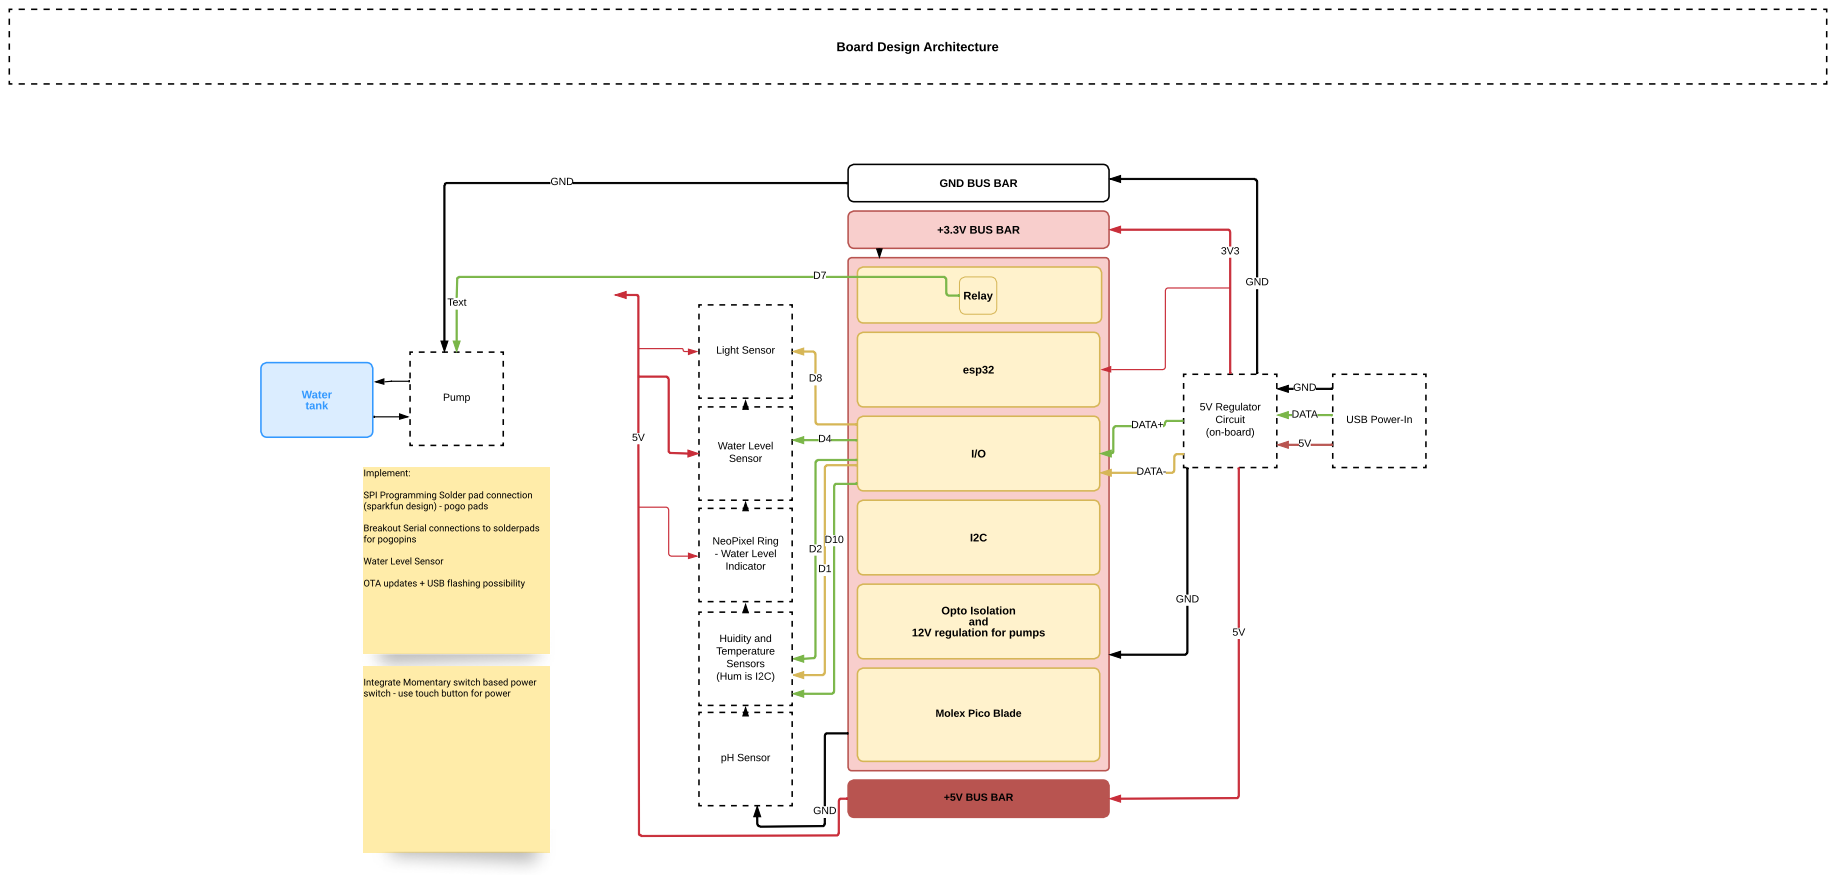
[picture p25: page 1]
ESP32HMS; esp32; Relay; +3.3V BUS BAR; Water; tank; 5V Regulator Circuit; (on-board); GND; DATA+; Water Level Sensor; NeoPixel Ring - Water Level Indicator; Pump; Light Sensor; Text; +5V BUS BAR; DATA-; Opto Isolation and; Huidity and Temperature Sensors (Hum is I2C); Implement:; pH Sensor

GND BUS BAR

USB Power-In DATA

SPI Programming Solder pad connection
(sparkfun design) - pogo pads

Breakout Serial connections to solderpads
for pogopins

Water Level Sensor

OTA updates + USB flashing possibility

12V regulation for pumps

Integrate Momentary switch based power
switch - use touch button for power

Molex Pico Blade

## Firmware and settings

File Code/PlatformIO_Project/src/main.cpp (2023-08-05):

// TODO: Implement observer for humidity sensor
// TODO: Implement pressure sensor for water level
// TODO: Implement IR sensor for water level
// TODO: Implement Home Assistant MQTT Support
// TODO: Implement feature flag to enable/disable Home Assistant MQTT Support
// TODO: Implement interfaces for the API - to use Serial, MQTT, HTTP, etc
// TODO: Abstract API using the bridge pattern
// TODO: Implement setting features using the API
// Note: default to the REST API if no mqtt feature is enabled
// Note: default to the basic mqtt if HASSIO support is disabled

#include <Arduino.h>

//* Utilities
#include <local/logo/logo.hpp>
#include <utilities/network_utilities.hpp>

//* Network
#include <local/network/api/rest_api.hpp>
#include <network/mdns/mdns_manager.hpp>
#include "local/network/mqtt/basic/basicmqtt.hpp"

//* Data
#include <local/data/accumulatedata/accumulatedata.hpp>
#include <local/data/config/config.hpp>

//*  Sensor Includes
#include <local/io/sensors/humidity/humidity.hpp>
#include <local/io/sensors/light/ldr.hpp>
#include <local/io/sensors/temperature/towertemp.hpp>
#include <local/io/sensors/water_level/waterlevelsensor.hpp>

//* Time stamp
#include <local/network/ntp/ntp.hpp>

//! Objects

//* Config
ProjectConfig config("greenhouse", "tower");
ConfigHandler configHandler(config);
GreenHouseConfig greenhouseConfig(config);

//* Network
WiFiHandler network(config, WIFI_SSID, WIFI_PASS, 1);
MDNSHandler mDNS(config, "_tower", "data", "_tcp", "api_port", "80");
NetworkNTP ntp;
MQTTClient mqttClient;
BaseMQTT mqtt(greenhouseConfig, config, mqttClient);

//* API
RestAPI rest_api(config, greenhouseConfig);

//* Sensors
TowerTemp tower_temp(greenhouseConfig);
Humidity humidity(greenhouseConfig);
WaterLevelSensor waterLevelSensor(tower_temp);
LDR ldr(greenhouseConfig);

//* Data
AccumulateData data(greenhouseConfig,
                    config,
                    ldr,
                    tower_temp,
                    humidity,
                    waterLevelSensor,
                    ntp,
                    mqtt);

void setup() {
  Serial.begin(115200);
  // Logo::printASCII();

  //* Setup Events and Background Tasks
  config.attach(configHandler);
  config.registerUserConfig(&greenhouseConfig);
  config.attach(network);
  config.attach(mDNS);  // attach the mDNS to the config manager

  //* Load Config from memory
  configHandler.begin();

  //* Setup Sensors
  humidity.begin();
  tower_temp.begin();

  //* Setup Network Tasks
  network.begin();
  mDNS.begin();
  mqtt.begin();
  rest_api.begin();
  ntp.begin();
}

/**
 * @brief Main Loop
 * The main loop is responsible for handling in the following order:
 * 1. WiFi State
 * 2. OTA Updates
 * 3. Accumulate Data
 * 4. Background Tasks
 */
void loop() {
  Network_Utilities::checkWiFiState();  // check the WiFi state
  data.loop();                          // accumulate sensor data
}

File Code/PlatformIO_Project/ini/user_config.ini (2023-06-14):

[time_zone_offset]
; 1    // Central European Time
; -5;  // Eastern Standard Time (USA)
; -4;  // Eastern Daylight Time (USA)
; -8;  // Pacific Standard Time (USA)
; -7;  // Pacific Daylight Time (USA)
time_zone_offset = 1

# This file is for user configuration

[sim]
ssid = "Wokwi-GUEST" # required for simulator
password = ""

[wifi]
ssid = "" 
password = ""
hostname = "esp32custom"
channel = 1
ap_ssid = "esp32custom"
ap_password = "12345678"
enableadhoc = 0
adhocchannel = 1

[ota]
enableota = 1
otaserverip = "esp32custom.local"
otapassword = "12345678"
otaserverport = 3232

[io]
relay_pin = 32
nozzle_pin = 33
echo_pin = 13
trig_pin = 14
one_wire_bus = 26

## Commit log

2021-09-03 Initial Commit
    commit-1
    [1-Way_Planting_Module.STL, 1-Way_Planting_Module_Hollow.STL, 1-Way_Planting_Module_Hollow_Without_M3.STL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]
2021-09-04 Organized Layout
    No file additions, simple organization
    [1-Way_Planting_Module.STL, 1-Way_Planting_Module_Hollow.STL, 1-Way_Planting_Module_Hollow_Without_M3.STL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]
2021-09-04 Create BOM_PCB_esp32G_2_2021-09-04.csv
    Upload the BOM for PCB files
    [BOM_PCB_esp32G_2_2021-09-04.csv]
2021-09-04 upload schematic and PCB image
2022-04-30 added DHT sensors and SHT31 selection logic
2022-04-30 fix I2C scanner
2022-05-02 add boiler-plate REST API code
2022-05-17 added MQTT sensor support
2022-05-17 moved ldr code to sensors dir and added advanced MQTT handling functions
2022-05-18 update water level detection using distance sensor
2022-05-18 begin to add logic for bh1750 light sensor and ir distance sensor
    Update platformio.ini with comments
2022-05-30 update HASSIO implementation - add support for 5 relays
2022-05-31 update
    - Remove Serial.println statements and replace with ESP log functions
2022-05-31 update
    - Add pH sensor to accumulate data and global file
    - Change all console logging to ESP log functions in basicmqtt
    - Add dynamic user controlled time-zone support for NTP server offset
2022-05-31 update
    - Add pump topic for MQTT
    - Add pH sensor pin setup
2022-05-31 update
    - Add pump class and logic to control
    - Move Relay pin setup to Relay class and out of Main
    - move NTP code to it's own class and fix all use-cases of it
    - Add NTP loop to TimedTasks to run in background ever 1 second
    [main.cpp]
2022-05-31 update
    - Implement complete logic for pump
2022-05-31 update
    - Reformat pump code
2022-05-31 update - critical
    - Add custom Atlas Scientific gravity sensor library, required to support the ESP32
2022-05-31 update
    - Add NTP service to background task class
    - Add mechanism to update pH sensor calibration from the Serial monitor
2022-05-31 update
    - Remove custom Atlas Sensor library, and move to github repo, add github repo link to ini file
2022-05-31 update
    -Refactor class folders
    - Implement Button class
2022-06-01 update
    - Edit Tower Temp class to properly get and set the number of sensors detected
    - Edited all calls and interfaces of the Tower Temp Class
2022-06-01 update
    - Delete unecessary global variables
    - Create getBroker Function to fail-over incase mDNS fails
    [main.cpp]
2022-06-01 update
    - Setup pump to not run during the night
    - fix classes
2022-06-01 update
    - Add preprocessor guards for PID control in Relay class
    - Optimize class constructors
2022-06-02 update
    - Remove redundant code from hassmqtt
    - Remove auto keyword from Relays.cpp
2022-06-02 update
    - update class constructor to timedtasks
    - Add callback to buttons class
2023-02-13 fix: cleanup project structure
    [user_config.ini]
2023-02-13 fix: begin refactoring code-base
    [config.cpp, main.cpp, pump.cpp]
2023-02-13 fix: migrate old files
    - create diagram of project
    [Oldmqtt.cpp, config.cpp, pump.cpp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]
2023-02-13 fix: continue refactoring code-base
    [user_config.ini]
2023-02-15 feat: i2c relay support
2023-02-15 fix: add start state to relays
2023-02-18 fix: begin to refactor mqtt stack
    [main.cpp]
2023-02-25 fix: continue making edits
    - add wokwi simulator support
    [main.cpp]
2023-02-26 refactor: continue refactoring codebase
    - simplifying
    - fixing classes
    - creating dependancy injections
    [main.cpp]
2023-02-26 fix: add timer to accumulatedata
    - format classes
2023-02-26 fix: continue working on mqtt stack
    [main.cpp]
2023-06-11 fix: begin simplifying and refactoring
    [main.cpp, pHsensor.cpp]
2023-06-12 fix: fixing compile time errors due to refactor
    [main.cpp]
2023-06-12 fix: enable mqtt loop
    [main.cpp]
2023-06-12 fix: github ignore case
2023-06-14 fix: continue fixing sensors
    - implemented wokwi simulator
    - setup support for esp32s3
    - finished sensor refactor
    [main.cpp, user_config.ini]
2023-06-14 refactor: switch to specialization for sensor serializer
2023-06-14 fix: bug in sensor serializer formatter
2023-06-15 fix: runtime crashing issue
    [main.cpp]
2023-06-17 fix: json formatting for humidity sensor
    [main.cpp]
2023-06-18 chore(minor): 1.0.0 [skip ci]
    ## 1.0.0 (2023-06-18)
    ### 🍕 Features
    * add background task handler ([7f9d965](https://github.com/ZanzyTHEbar/ESP32GreenhouseTowerDIY/commit/7f9d9652ec51188cecebfd2e776007dd5767e54a))
    * add logo to serial console ([169f136](https://github.com/ZanzyTHEbar/ESP32GreenhouseTowerDIY/commit/169f136b43dbdc34171118e671f1ee006935b9f4))
    * add removeRelay ([aa6b9fd](https://github.com/ZanzyTHEbar/ESP32GreenhouseTowerDIY/commit/aa6b9fdf42b4f89757626d063ef28ee81243c39f))
    * begin adding config ([247ad1b](https://github.com/ZanzyTHEbar/ESP32GreenhouseTowerDIY/commit/247ad1b8340b6e50109b7cb38dd77d7dc162f690))
    * begin adding support for HASSIO ([f4a4006](https://github.com/Z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
2023-06-18 chore(minor): 1.1.0 [skip ci]
    ## [1.1.0](https://github.com/ZanzyTHEbar/ESP32GreenhouseTowerDIY/compare/v1.0.0...v1.1.0) (2023-06-18)
    ### 📝 Documentation
    * Update README.md ([b944241](https://github.com/ZanzyTHEbar/ESP32GreenhouseTowerDIY/commit/b9442412ac55b0a36576bca5d22c3aadfa2c6640))
2023-06-20 chore(patch): 1.1.1 [skip ci]
    ## [1.1.1](https://github.com/ZanzyTHEbar/ESP32GreenhouseTowerDIY/compare/v1.1.0...v1.1.1) (2023-06-20)
    ### 🧑‍💻 Code Refactoring
    * cleanup serializer ([f33a53d](https://github.com/ZanzyTHEbar/ESP32GreenhouseTowerDIY/commit/f33a53db516d198f2b167e444611039c36365094))
2023-06-20 chore(patch): 1.1.2 [skip ci]
    ## [1.1.2](https://github.com/ZanzyTHEbar/ESP32GreenhouseTowerDIY/compare/v1.1.1...v1.1.2) (2023-06-20)
    * Update user_config.ini ([a0a9ad5](https://github.com/ZanzyTHEbar/ESP32GreenhouseTowerDIY/commit/a0a9ad5e9ebc33352586a8f6efbfea676100db00))
    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
2023-06-20 chore(patch): 1.1.3 [skip ci]
    ## [1.1.3](https://github.com/ZanzyTHEbar/ESP32GreenhouseTowerDIY/compare/v1.1.2...v1.1.3) (2023-06-20)
    ### 🐛 Bug Fixes
    * bug in serializer ([8999751](https://github.com/ZanzyTHEbar/ESP32GreenhouseTowerDIY/commit/8999751c1dfa226e95007fec7c210f5b7b87d3ce))
2023-06-20 chore(minor): 1.2.0 [skip ci]
    ## [1.2.0](https://github.com/ZanzyTHEbar/ESP32GreenhouseTowerDIY/compare/v1.1.3...v1.2.0) (2023-06-20)
    * begin working on the API ([271a828](https://github.com/ZanzyTHEbar/ESP32GreenhouseTowerDIY/commit/271a8285c2cfdbf2701d9e2129c0c9203dac1db0))
    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
